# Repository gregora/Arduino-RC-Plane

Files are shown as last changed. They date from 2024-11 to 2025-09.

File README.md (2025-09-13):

# Arduino-RC-Plane
An RC airplane, controlled by a custom flight controller based on Arduino Nano.

## CAD

CAD files are available on OnShape [here](https://cad.onshape.com/documents/968e81f1afc8243e275bf7ca/w/acaf7929af669ea720083764/e/5f49399fe13c6903e510c987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)

## Controller hardware

The following devices are necessary to recreate the flight controller:
* Arduino Nano microcontroller
* BNO055 Adafruit absolute orientation sensor
* CC1101 radio module

* Flysky radio receiver (or any receiver with iBus)

## Flight modes

The controller enables you to choose from a few different modes of flying. A mode of flying can be chosen by flipping a switch on your radio transmitter on channel 6.

* `Mode 0 - Manual`: Your transmitter outputs are directly linked to the motors.
* `Mode 1 - Take-off`: The aircraft will maintain a 10 degree pitch-up with wings level.
* `Mode 2 - Fly-by-wire` - The aircraft will follow the angular velocity, commanded by the transmitter. For example, a full deflection  of right joystick corresponds to `2*pi rad/s` roll rate.
* `Mode 3 - Automatic` - The aircraft will fly automatically to the desired target position
* `Mode 255 - Recovery`: The aircraft will assume -10 degree pitch down and wings level

## Ground UI

UI for ground control was also written in Python. The UI includes all the necessary information about the flight and enables saving the flight data to a csv file.

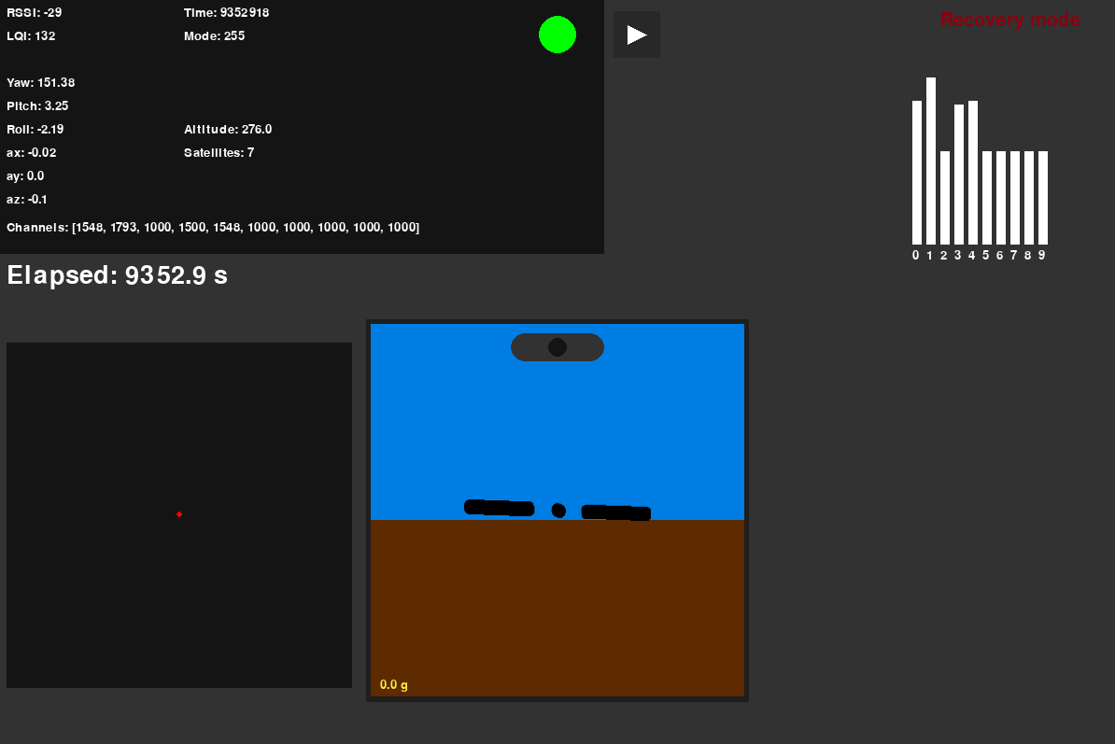
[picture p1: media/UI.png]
Ground UI


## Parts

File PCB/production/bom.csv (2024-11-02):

Designator | Footprint | Quantity | Value | LCSC Part #
A1 | Arduino_Nano | 1 | Arduino_Nano_Every
J1 | PinSocket_1x06_P2.54mm_Vertical | 1 | Conn_01x06_Pin
J2 | PinSocket_1x04_P2.54mm_Vertical | 1 | Conn_01x04_Pin
J3 | PinHeader_1x03_P2.54mm_Vertical | 1 | Conn_01x03
J4 | PinSocket_2x04_P2.54mm_Vertical | 1 | Conn_02x04_Odd_Even
J5 | PinHeader_1x03_P2.54mm_Vertical | 1 | GPIO7
J6 | PinHeader_1x03_P2.54mm_Vertical | 1 | GPIO8
J7 | PinHeader_1x03_P2.54mm_Vertical | 1 | GPIO9
M1, M2, M3, M4, M5 | PinHeader_1x03_P2.54mm_Vertical | 5 | Motor_Servo

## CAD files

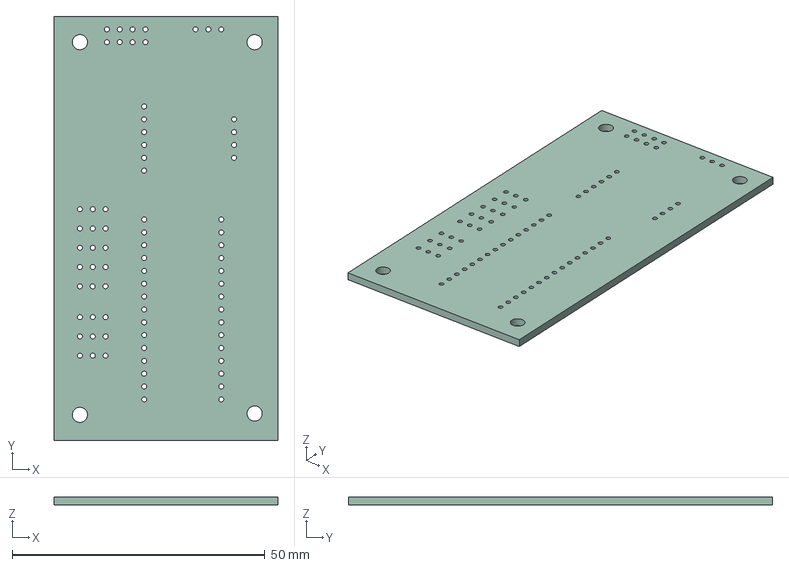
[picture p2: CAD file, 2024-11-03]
PCB/PlaneController.step
44.2 x 83.8 x 1.60 mm

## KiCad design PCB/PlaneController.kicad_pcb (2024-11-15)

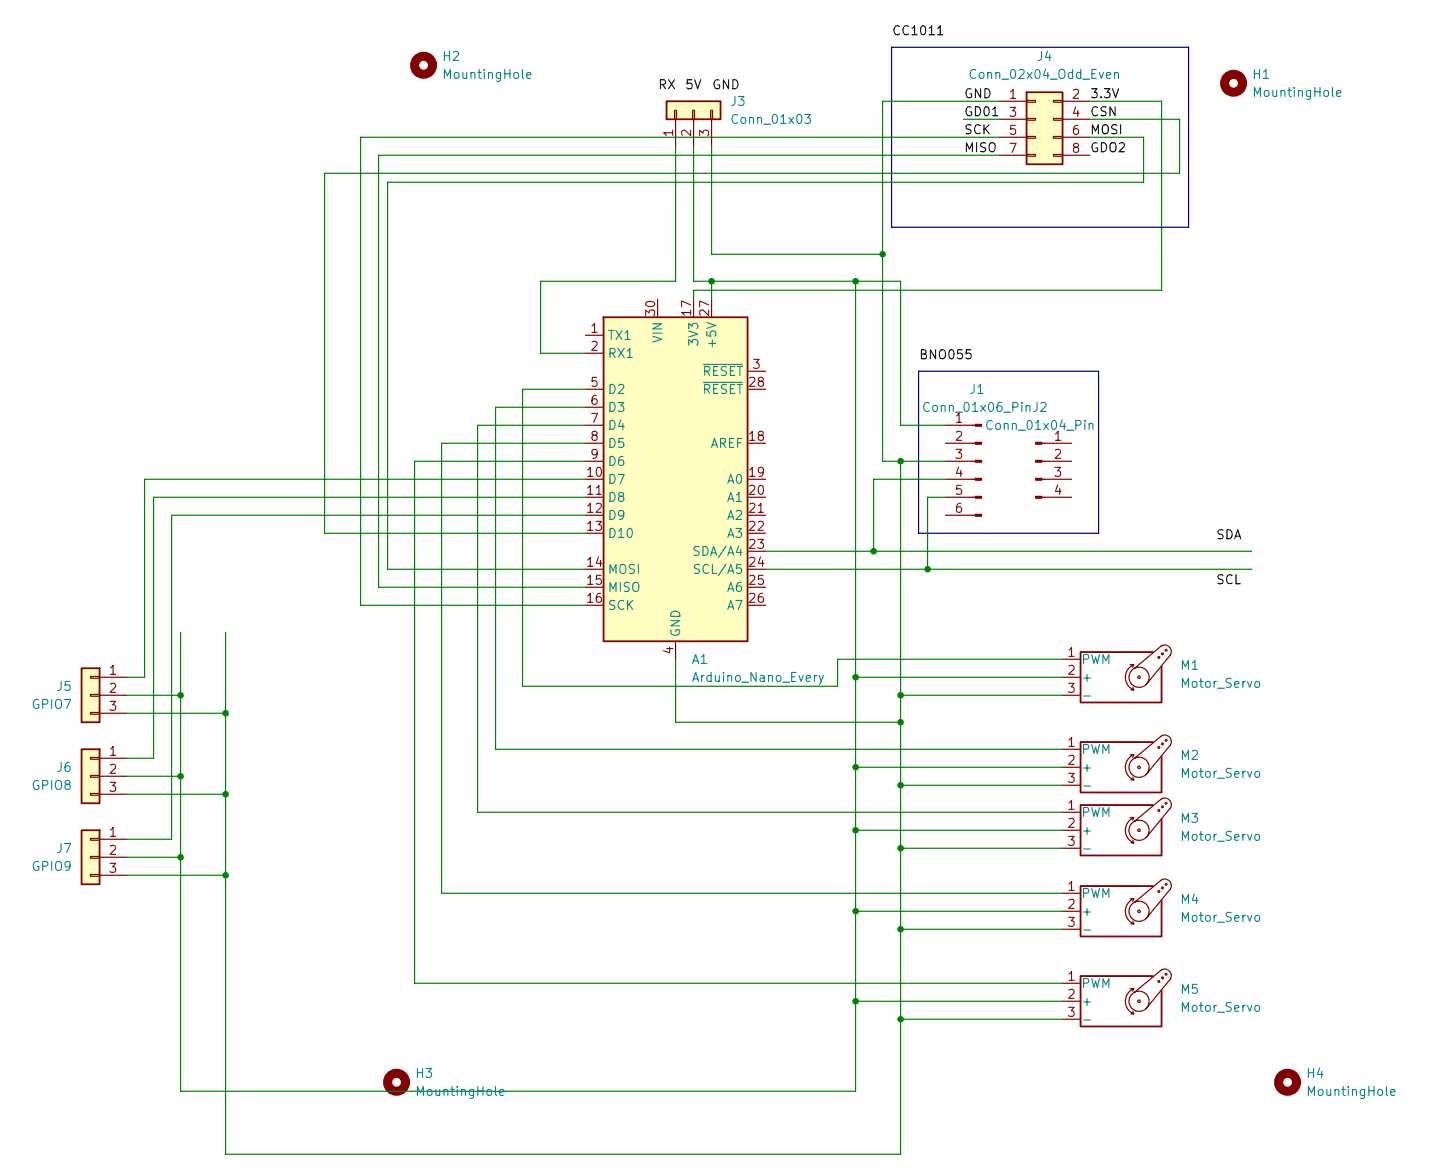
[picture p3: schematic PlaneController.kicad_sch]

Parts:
A1: Arduino_Nano_Every; Arduino_Nano
H1, H2, H3, H4: MountingHole; MountingHole_3mm
J1: Conn_01x06_Pin; PinSocket_1x06_P2.54mm_Vertical
J2: Conn_01x04_Pin; PinSocket_1x04_P2.54mm_Vertical
J3: Conn_01x03; PinHeader_1x03_P2.54mm_Vertical
J4: Conn_02x04_Odd_Even; PinSocket_2x04_P2.54mm_Vertical
J5: GPIO7; PinHeader_1x03_P2.54mm_Vertical
J6: GPIO8; PinHeader_1x03_P2.54mm_Vertical
J7: GPIO9; PinHeader_1x03_P2.54mm_Vertical
M1, M2, M3, M4, M5: Motor_Servo; PinHeader_1x03_P2.54mm_Vertical

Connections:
/3.3V: A1.17 (3V3), J4.2
/CSN: A1.13 (D10), J4.4
/GD01: J4.3
/GDO2: J4.8
/GND: A1.4 (GND), A1.29 (GND), J1.3, J3.3, J4.1, J5.3, J6.3, J7.3, M1.3 (-), M2.3 (-), M3.3 (-), M4.3 (-), M5.3 (-)
/MISO: A1.15 (MISO), J4.7
/MOSI: A1.14 (MOSI), J4.6
/SCK: A1.16 (SCK), J4.5
unnamed: A1.27 (+5V), J1.1, J3.2, J5.2, J6.2, J7.2, M1.2 (+), M2.2 (+), M3.2 (+), M4.2 (+), M5.2 (+)
unnamed: A1.5 (D2), M1.1 (PWM)
unnamed: A1.6 (D3), M2.1 (PWM)
unnamed: A1.7 (D4), M3.1 (PWM)
unnamed: A1.8 (D5), M4.1 (PWM)
unnamed: A1.9 (D6), M5.1 (PWM)
unnamed: A1.10 (D7), J5.1
unnamed: A1.11 (D8), J6.1
unnamed: A1.12 (D9), J7.1
unnamed: A1.2 (RX1), J3.1
unnamed: A1.24 (SCL/A5), J1.5
unnamed: A1.23 (SDA/A4), J1.4

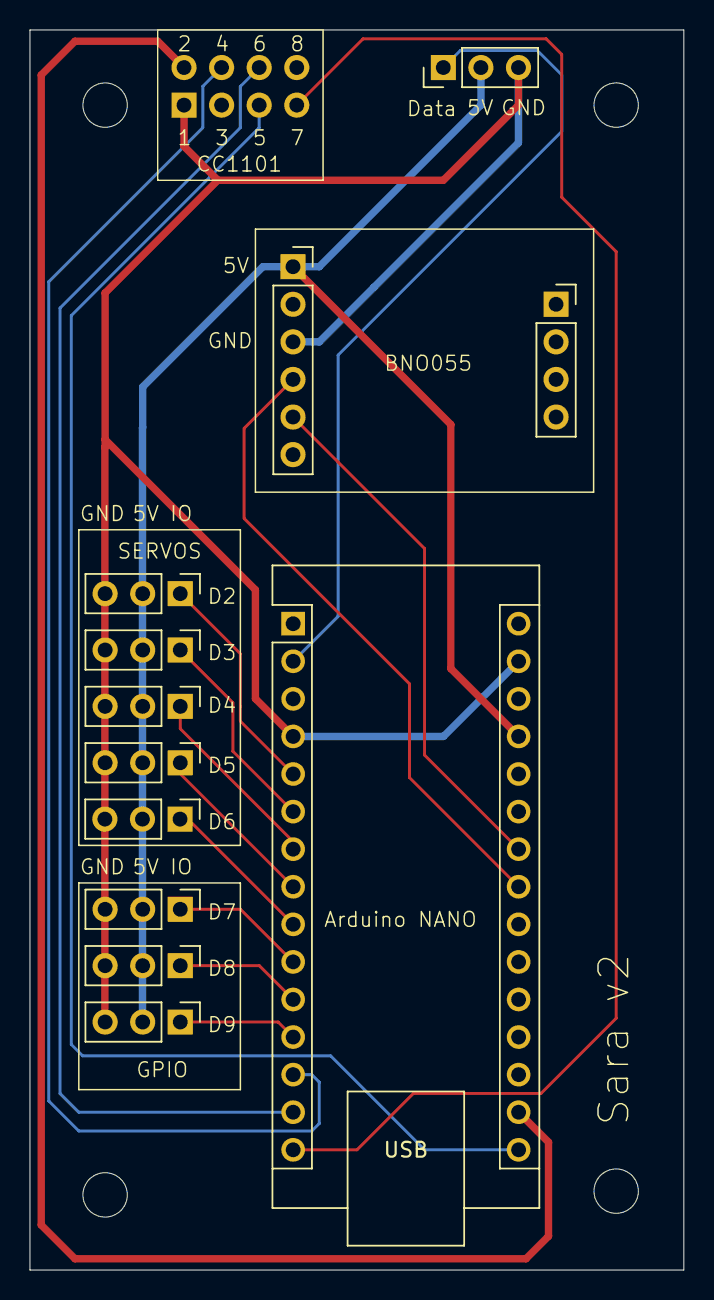
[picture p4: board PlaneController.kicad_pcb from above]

Board: 2 copper layers, 44.2 x 83.8 mm, 17 parts (1 on the bottom side), 18 nets.

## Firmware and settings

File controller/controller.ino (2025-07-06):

#include <Wire.h>
#include <Adafruit_Sensor.h>

#include <Adafruit_BNO055.h>
#include <Servo.h>

#include <IBusBM.h>

#include <ELECHOUSE_CC1101_SRC_DRV.h>

#include <TinyGPS++.h>
#include <SoftwareSerial.h>

//Servo ch1;
//Servo ch2;
//Servo ch3;
//Servo ch4;
//Servo ch5;

Adafruit_BNO055 bno = Adafruit_BNO055(55);

IBusBM IBus;

TinyGPSPlus gps;
SoftwareSerial ss(7, 8); // GPS


#define DEBUG false
#define PERFORMANCE false
#define ANG_VEL false
#define MAG false
#define GPS false

bool bno_status = false;
bool ibus_status = false;
bool cc1101_status = false;

unsigned int frame = 0;

struct Packet {
  unsigned long time;

  imu::Quaternion quat; // orientation quaternion

  float ax;
  float ay;
  float az;

  float latitude;
  float longitude;
  int altitude; // gps altitude in meters

  int satellites; // number of satellites

  int channels[7];


  /*
  MODES:
  0 - manual
  1 - take-off
  2 - fly-by-wire

  255 - recovery
  */
  int mode;

};



float yaw;
float pitch;
float roll;


float ang_yaw;
float ang_pitch;
float ang_roll;

Packet p;

float fixes = 0;


void setup() {
  p.mode = 0;

  // attach the motors to corresponding pins
  //ch1.attach(2);
  //ch2.attach(3);
  //ch3.attach(4);
  //ch4.attach(5);
  //ch5.attach(6);

  pinMode(3, OUTPUT);
  //pinMode(5, OUTPUT);
  //pinMode(6, OUTPUT);
  pinMode(9, OUTPUT);


  if(DEBUG){
    Serial.begin(115200);
  }

  IBus.begin(Serial, IBUSBM_NOTIMER); // use Serial to read flysky receiver iBUS

  if(!bno.begin()){
    bno_status = false;
    if(DEBUG){
      Serial.println("BNO055: Connection ERROR");
    }
  }else {
    bno_status = true;
  
    delay(1000);

    bno.setExtCrystalUse(true);
  }


  if (!ELECHOUSE_cc1101.getCC1101()){        // Check the CC1101 Spi connection.
    cc1101_status = false;
    if(DEBUG){
      Serial.println("CC1101: Connection ERROR");
    }
  }else{
    cc1101_status = true;
  }


  ss.begin(9600);

  // Disable NMEA
  byte sentances [][16] = {
    //{0xB5,0x62,0x06,0x01,0x08,0x00,0xF0,0x00,0x00,0x00,0x00,0x00,0x00,0x01,0x00,0x24}, // GxGGA off
    {0xB5,0x62,0x06,0x01,0x08,0x00,0xF0,0x01,0x00,0x00,0x00,0x00,0x00,0x01,0x01,0x2B}, // GxGLL off
    {0xB5,0x62,0x06,0x01,0x08,0x00,0xF0,0x02,0x00,0x00,0x00,0x00,0x00,0x01,0x02,0x32}, // GxGSA off
    {0xB5,0x62,0x06,0x01,0x08,0x00,0xF0,0x03,0x00,0x00,0x00,0x00,0x00,0x01,0x03,0x39}, // GxGSV off
    {0xB5,0x62,0x06,0x01,0x08,0x00,0xF0,0x04,0x00,0x00,0x00,0x00,0x00,0x01,0x04,0x40}, // GxRMC off
    {0xB5,0x62,0x06,0x01,0x08,0x00,0xF0,0x05,0x00,0x00,0x00,0x00,0x00,0x01,0x05,0x47} // GxVTG off
  };

  for (unsigned int j = 0; j < sizeof(sentances); j++){
    for(unsigned int i = 0; i < sizeof(sentances[i]); i++) {  
      ss.write(sentances[j][i]);
    }
  }

  const unsigned char UBLOX_INIT[] PROGMEM = {
      //0xB5,0x62,0x06,0x08,0x06,0x00,0x64,0x00,0x01,0x00,0x01,0x00,0x7A,0x12, //(10Hz)
      0xB5,0x62,0x06,0x08,0x06,0x00,0xC8,0x00,0x01,0x00,0x01,0x00,0xDE,0x6A //(5Hz)
      //0xB5,0x62,0x06,0x08,0x06,0x00,0xE8,0x03,0x01,0x00,0x01,0x00,0x01,0x39 //(1Hz)
    };

  // send configuration data in UBX protocol
  for(unsigned int i = 0; i < sizeof(UBLOX_INIT); i++) {                        
    ss.write(UBLOX_INIT[i]); // 5Hz refresh rate
  }


  // change baudrate to 19200
  ss.write("$PUBX,41,1,0007,0003,19200,0*25\r\n");
  ss.flush();
  ss.end();

  delay(500);

  ss.begin(19200);




  



  ELECHOUSE_cc1101.Init();              // must be set to initialize the cc1101!
  ELECHOUSE_cc1101.setCCMode(1);       // set config for internal transmission mode.
  ELECHOUSE_cc1101.setModulation(0);  // set modulation mode. 0 = 2-FSK, 1 = GFSK, 2 = ASK/OOK, 3 = 4-FSK, 4 = MSK.
  ELECHOUSE_cc1101.setMHZ(433.92);   // Here you can set your basic frequency. The lib calculates the frequency automatically (default = 433.92).The cc1101 can: 300-348 MHZ, 387-464MHZ and 779-928MHZ. Read More info from datasheet.
  ELECHOUSE_cc1101.setSyncMode(2);  // Combined sync-word qualifier mode. 0 = No preamble/sync. 1 = 16 sync word bits detected. 2 = 16/16 sync word bits detected. 3 = 30/32 sync word bits detected. 4 = No preamble/sync, carrier-sense above threshold. 5 = 15/16 + carrier-sense above threshold. 6 = 16/16 + carrier-sense above threshold. 7 = 30/32 + carrier-sense above threshold.
  // ELECHOUSE_cc1101.setPA(10);      // set TxPower. The following settings are possible depending on the frequency band.  (-30  -20  -15  -10  -6    0    5    7    10   11   12) Default is max!
  ELECHOUSE_cc1101.setCrc(1);     // 1 = CRC calculation in TX and CRC check in RX enabled. 0 = CRC disabled for TX and RX.


}


void loop() {

  frame++;

  unsigned long t1 = millis();

  if(bno_status){
  

    // read BNO055 attitude data
    imu::Vector<3> vector1;
    vector1 = bno.getVector(Adafruit_BNO055::VECTOR_EULER);

    p.quat = bno.getQuat();
    vector1 = p.quat.toEuler();
    yaw   = vector1.x() * 180 / 3.1415; 
    pitch = vector1.y() * 180 / 3.1415;
    roll  = vector1.z() * 180 / 3.1415;

    // read BNO055 lateral accelerations
    imu::Vector<3> vector2;
    vector2 = bno.getVector(Adafruit_BNO055::VECTOR_LINEARACCEL);

    p.ax = vector2.x();
    p.ay = vector2.y();
    p.az = vector2.z();


    // read BNO055 angular velocities
    imu::Vector<3> vector3;
    vector3 = bno.getVector(Adafruit_BNO055::VECTOR_GYROSCOPE);
    ang_roll = vector3.x();
    ang_pitch = vector3.y();
    ang_yaw = vector3.z();
    
    //  read BNO055 magnetometer
    imu::Vector<3> vector4;
    vector4 = bno.getVector(Adafruit_BNO055::VECTOR_MAGNETOMETER);
    float mag_x = vector4.x();
    float mag_y = vector4.y();
    float mag_z = vector4.z();

    if(DEBUG && ANG_VEL){
      Serial.print(ang_roll);
      Serial.print(" ");
      Serial.print(ang_pitch);
      Serial.print(" ");
      Serial.print(ang_yaw);
      Serial.println();
    }

    if(DEBUG && MAG) {
      Serial.print(mag_x);
      Serial.print(" ");
      Serial.print(mag_y);
      Serial.print(" ");
      Serial.print(mag_z);
      Serial.println();
      Serial.println(atan2(mag_y, mag_x) * 180 / 3.1415 + 180);

    }

  } else {
    p.mode = 0; // IMU unavailable - default to manual mode
  }


  unsigned long t2 = millis();

  while (ss.available() > 0){
    gps.encode(ss.read());
    //Serial.write(ss.read());
  }

  if (gps.location.isUpdated()){


    p.latitude = gps.location.lat();
    p.longitude = gps.location.lng();
    p.altitude = gps.altitude.meters();

    p.satellites = gps.satellites.value();

    if (DEBUG && GPS){
      Serial.print("Latitude= "); 
      Serial.print(p.latitude, 6);
      Serial.print(" Longitude= "); 
      Serial.print(p.longitude, 6);
      Serial.print(" Altitude= ");
      Serial.print((float) p.altitude, 0);
      Serial.print(" Satellites= ");
      Serial.println(p.satellites);
    
    
      fixes++;
      Serial.print("Fixes per second: ");
      Serial.println(fixes / p.time * 1000);
    }
  }

  unsigned long t3 = millis();

  IBus.loop();
  // read flysky receiver data
  for(int i = 0; i < 7; i++){
    p.channels[i] = IBus.readChannel(i);
  }

  // if any channel is 0, iBus is disconnected
  if(p.channels[6] != 0){ //check only for channel 6
    ibus_status = true;
    if(p.channels[6] == 2000){
      p.mode = 1;
    }else{
      p.mode = 0;
    }
  } else {
    ibus_status = false;
    p.mode = 255; // iBus is unavailable, enter recovery mode
  }


  if(p.mode == 1) {
    // take-off mode
    // target 10 deg nose up, wings level

    float P = 2000 / 90; // max deflection at 90 deg error
    float D = 50 / (4 * 3.14); // max deflection at 4*pi rad/s angular velocity

    p.channels[1] = 1500 + (pitch - 10) * P + ang_pitch*D;

    p.channels[0] = 1500 - roll*P - ang_roll*D;
    p.channels[4] = 1500 - roll*P - ang_roll*D;

    p.channels[3] = 1500;

  } else if(p.mode == 2){
    // fly-by-wire mode
    // target angular velocities

    float D = 100 / (8 * 3.14); // max deflection is at 8*pi rad/s angular velocity error

    // max desired angular velocity is 2*pi rad/s
    p.channels[1] = ((p.channels[1] - 1500) * 2*3.14 / 500 + ang_pitch) * D;

    p.channels[0] = ((p.channels[0] - 1500) * 2*3.14 / 500 - ang_roll) * D;
    p.channels[4] = ((p.channels[3] - 1500) * 2*3.14 / 500 - ang_roll) * D;

    p.channels[3] = 1500;

  }else if(p.mode == 255){  
    // recovery mode
    // target 10 deg nose down, wings level

    float P = 4.0 / 90         * 500; // max deflection at 90 deg error
    float D = 0.1 / (4 * 3.14) * 500; // max deflection at 4*pi rad/s angular velocity

    p.channels[1] = 1500 + (pitch + 10) * P + ang_pitch*D;

    p.channels[0] = 1500 - roll*P - ang_roll*D;
    p.channels[4] = 1500 - roll*P - ang_roll*D;

    p.channels[3] = 1500;
  }

  // limit the travel of servos
  // channels have min of 1000 and max 2000

  for(int i = 0; i < 7; i++){
    if(p.channels[i] < 1000){
      p.channels[i] = 1000;
    }

    if(p.channels[i] > 2000){
      p.channels[i] = 2000;
    }
  }


  // write received values to servos
  
  //ch1.writeMicroseconds(p.channels[0]); // aileron 1
  //ch2.writeMicroseconds(p.channels[1]); // elevator
  //ch3.writeMicroseconds(p.channels[2]); // throttle
  //ch4.writeMicroseconds(p.channels[3]); // rudder
  //ch5.writeMicroseconds(p.channels[4]); // aileron 2
  
  
  analogWrite(3, ((float) p.channels[0])*255.0/2000); // both ailerons
  //analogWrite(5, ((float) p.channels[3])*255.0/2000); // rudder
  analogWrite(9, ((float) p.channels[1])*255.0/2000); // horizontal stabilizer

  

  unsigned long t4 = millis();

  p.time = millis();

  // send data over radio (CC1101)
  if(cc1101_status){
    ELECHOUSE_cc1101.SendData((void*) &p, sizeof(p), 8);
  }

  unsigned long t5 = millis();

  if(DEBUG && PERFORMANCE){
    Serial.println("DEBUG: Performance");

    Serial.print("  IMU: ");
    Serial.println(t2 - t1);

    Serial.print("  GPS: ");
    Serial.println(t3 - t2);


    Serial.print("  iBUS: ");
    Serial.println(t4 - t3);

    Serial.print("  Telemetry: ");
    Serial.println(t5 - t4);

    Serial.println();
  }

}

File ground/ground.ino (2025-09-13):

#include <Wire.h>

#include <Adafruit_Sensor.h>

#include <Adafruit_BNO055.h>

#include <ELECHOUSE_CC1101_SRC_DRV.h>


struct Packet {
  unsigned long time;

  imu::Quaternion quat; // orientation quaternion

  float ax;
  float ay;
  float az;

  float latitude;
  float longitude;
  int altitude; // gps altitude in meters

  int satellites; // number of satellites

  int channels[7];


  /*
  MODES:
  0 - manual
  1 - take-off
  2 - fly-by-wire

  255 - recovery
  */
  int mode;

};

float yaw;
float pitch;
float roll;


Packet p;

// Seems to be the same as Adafruit's implementation
void quat2ZYX(imu::Quaternion q, float &yaw, float &pitch, float &roll) {
  double sinr_cosp = 2 * (q.w() * q.x() + q.y() * q.z());
  double cosr_cosp = 1 - 2 * (q.x() * q.x() + q.y() * q.y());
  roll = atan2(sinr_cosp, cosr_cosp);

  // pitch (y-axis rotation)
  double sinp = sqrt(1 + 2 * (q.w() * q.y() - q.x() * q.z()));
  double cosp = sqrt(1 - 2 * (q.w() * q.y() - q.x() * q.z()));
  pitch = 2 * atan2(sinp, cosp) - M_PI / 2;

  // yaw (z-axis rotation)
  double siny_cosp = 2 * (q.w() * q.z() + q.x() * q.y());
  double cosy_cosp = 1 - 2 * (q.y() * q.y() + q.z() * q.z());
  yaw = atan2(siny_cosp, cosy_cosp);

  // Convert radians to degrees
  yaw   *= 180 / 3.1415;
  pitch *= 180 / 3.1415;
  roll  *= 180 / 3.1415;
}

void printPacket(Packet p){

  imu::Vector<3> euler;
  euler = p.quat.toEuler();

  yaw   = euler.x() * 180 / 3.1415;
  pitch = euler.y() * 180 / 3.1415;
  roll  = euler.z() * 180 / 3.1415;

  // Works the same as .toEuler()
  //quat2ZYX(p.quat, yaw, pitch, roll);

  Serial.print("Time: ");
  Serial.println(p.time);

  Serial.print("Yaw: ");
  Serial.println(yaw, 4);

  Serial.print("Pitch: ");
  Serial.println(pitch, 4);

  Serial.print("Roll: ");
  Serial.println(roll, 4);

  Serial.print("q1: ");
  Serial.println(p.quat.w(), 10);

  Serial.print("q2: ");
  Serial.println(p.quat.x(), 10);

  Serial.print("q3: ");
  Serial.println(p.quat.y(), 10);

  Serial.print("q4: ");
  Serial.println(p.quat.z(), 10);

  // max precision for acceleration is 2 decimals
  Serial.print("ax: ");
  Serial.println(p.ax, 2);

  Serial.print("ay: ");
  Serial.println(p.ay, 2);

  Serial.print("az: ");
  Serial.println(p.az, 2);

  Serial.print("Latitude: ");
  Serial.println(p.latitude, 10);

  Serial.print("Longitude: ");
  Serial.println(p.longitude, 10);

  Serial.print("Altitude: ");
  Serial.println((float) p.altitude, 3);

  Serial.print("Satellites: ");
  Serial.println(p.satellites);
  
  Serial.print("Channels: \n");
  for(int i = 0; i < 7; i++){
    Serial.print(p.channels[i]);
    Serial.print(" ");
  }
  Serial.println();

  Serial.print("Mode: ");
  Serial.println((int) p.mode);

}

void setup() {

  Serial.begin(115200);  // start serial for output

  if (ELECHOUSE_cc1101.getCC1101()){        // Check the CC1101 Spi connection.
    Serial.println("CC1101: Connection OK");
  }else{
    Serial.println("CC1101: Connection ERROR");
  }

  ELECHOUSE_cc1101.Init();              // must be set to initialize the cc1101!
  ELECHOUSE_cc1101.setCCMode(1);       // set config for internal transmission mode.
  ELECHOUSE_cc1101.setModulation(0);  // set modulation mode. 0 = 2-FSK, 1 = GFSK, 2 = ASK/OOK, 3 = 4-FSK, 4 = MSK.
  //ELECHOUSE_cc1101.setDRate(2.4);
  ELECHOUSE_cc1101.setMHZ(433.92);   // Here you can set your basic frequency. The lib calculates the frequency automatically (default = 433.92).The cc1101 can: 300-348 MHZ, 387-464MHZ and 779-928MHZ. Read More info from datasheet.
  ELECHOUSE_cc1101.setSyncMode(2);  // Combined sync-word qualifier mode. 0 = No preamble/sync. 1 = 16 sync word bits detected. 2 = 16/16 sync word bits detected. 3 = 30/32 sync word bits detected. 4 = No preamble/sync, carrier-sense above threshold. 5 = 15/16 + carrier-sense above threshold. 6 = 16/16 + carrier-sense above threshold. 7 = 30/32 + carrier-sense above threshold.
  ELECHOUSE_cc1101.setCrc(1);      // 1 = CRC calculation in TX and CRC check in RX enabled. 0 = CRC disabled for TX and RX.



  for (int i = 0x04; i <= 0x28; i++){
    uint8_t reg = ELECHOUSE_cc1101.SpiReadReg(i);
    Serial.print("TI_write_reg(0x");
    Serial.print(i, HEX);
    Serial.print(", 0x");
    Serial.print(reg, HEX);
    Serial.print(");\n");
  }


    int i = 0x3E;
    uint8_t reg = ELECHOUSE_cc1101.SpiReadReg(i);
    Serial.print("TI_write_reg(0x");
    Serial.print(i, HEX);
    Serial.print(", 0x");
    Serial.print(reg, HEX);
    Serial.print(");\n");



}

void loop() {
    //return;
    //Checks whether something has been received.
    //When something is received we give some time to receive the message in full.(time in millis)
    if (ELECHOUSE_cc1101.CheckRxFifo(8)){
      
     
      if (ELECHOUSE_cc1101.CheckCRC()){    //CRC Check. If "setCrc(false)" crc returns always OK!
        
        Serial.println("GND PACKET");
        Serial.print("Rssi: ");
        Serial.println(ELECHOUSE_cc1101.getRssi());
        Serial.print("LQI: ");
        Serial.println(ELECHOUSE_cc1101.getLqi());
        
        int len = ELECHOUSE_cc1101.ReceiveData((void*) &p);

        printPacket(p);

        Serial.println();

      }
    }
}

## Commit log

2024-08-17 Add PCB and CAD files
    [PlaneController-B_Cu.gbr, PlaneController-B_Mask.gbr, PlaneController-B_Silks.gbr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]
2024-08-24 Add 5th servo
    [PlaneController.kicad_pcb]
2024-08-24 Remove PCB locks
2024-08-31 Add RX and TX connections to connect to receiver via iBUS
    [PlaneController.kicad_pcb, PlaneController.kicad_sch]
2024-09-11 Move files
    [SimpleAirplaneV1.0.FCStd, SimpleAirplaneV1.stl, SimpleAirplaneV1_Brackets.3mf]
2024-09-11 Improve PCB footprint
    [PlaneController.kicad_pcb]
2024-09-27 Add connection to receiver using 3x1 pin for iBUS, Vcc and GND
    [PlaneController.kicad_pcb, PlaneController.kicad_sch, PlaneController.step]
2024-09-28 Add PCB traces for CC1101 radio
    [PlaneController.kicad_pcb, PlaneController.kicad_sch]
2024-09-28 Read channels from IBus and send it to ground stations (via I2C)
2024-09-28 Minor changes
    [PlaneController.kicad_pcb]
2024-09-28 Major PCB fix
    [PlaneController.kicad_pcb, PlaneController.kicad_sch]
2024-09-28 Optimize PCB traces and update code
2024-11-02 Radio is now connected and unnecessary connections are removed from the pcb
    [PlaneController.kicad_pcb, PlaneController.kicad_sch]
2024-11-02 Add 3 more GPIO pins to the main PCB
    [PlaneController.kicad_pcb, PlaneController.kicad_sch]
2024-11-02 Add 3 more GPIO ports
    [PlaneController-B_Cu.gbr, PlaneController-B_Mask.gbr, PlaneController-B_Paste.gbp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]
2024-11-03 Add ground station code
    [PlaneController.kicad_pcb, PlaneController.step]
2024-11-04 Add button for recording
2024-11-06 Improve ground station packet handling as well
2024-11-07 Read angular velocities from BNO055
2024-11-10 Add fly-by-wire
2024-11-11 IMU failure - default to manual mode
    [controller.ino]
2024-11-12 Implement Fly-by-wire mode
2024-11-15 Fix bug in pcb
    [PlaneController.kicad_pcb]
2024-12-05 Partially fix servo jitter bug by removing iBus interrupts
    [controller.ino]
2024-12-07 Fix jittering by moving servos manually using analogWrite
    [controller.ino]
2025-02-19 Add magnetometer reading
2025-02-25 Set GPS speed to 5Hz and remove unnecessary sentances
2025-02-25 Ground software fixes and optimizations
    [controller.ino, ground.py]
2025-02-26 Add minimap display for ground station
2025-02-26 Bug fixes on UI
    [ground.py]
2025-03-13 Bug fixes in distance calculations from GPS
    [ground.py]
2025-04-18 Compute number of fixes per second
    [controller.ino]
2025-07-06 Update Packet class so there are no issues with alignment
    [controller.ino, ground.ino]
2025-07-30 Update ground station
